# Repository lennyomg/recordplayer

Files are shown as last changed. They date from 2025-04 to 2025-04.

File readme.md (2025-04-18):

# Record Player

A real player that plays fake records.

(https://www.youtube.com/watch?v=qOQR8iDCI8Y)

This is [Owntone](https://owntone.github.io/owntone-server/) media server in retro-style body. It plays local files and streams Spotify to local speakers or Apple HomePods. Disks are NFC tags. A Python application connects the NFC reader, LED lights, input controls, and controls Owntone using its RESTful API. Everything is running on a headless Raspberry Pi with a little help from a CircuitPython development board. And a small motor inside spins a disk.

[How to build](docs/instruction.md)
[Instructables](https://www.instructables.com/Record-Player-a-Real-Player-That-Plays-Fake-Record/)
[MakerWorld](https://makerworld.com/en/models/1300993-record-player)
[YouTube](https://www.youtube.com/watch?v=qOQR8iDCI8Y)
[OnShape](https://cad.onshape.com/documents/8d49c69d5558d4a3c2d04c2c/w/57560bbfb3612a29b81fb9af/e/d4a23e81e34f632615be4a04)

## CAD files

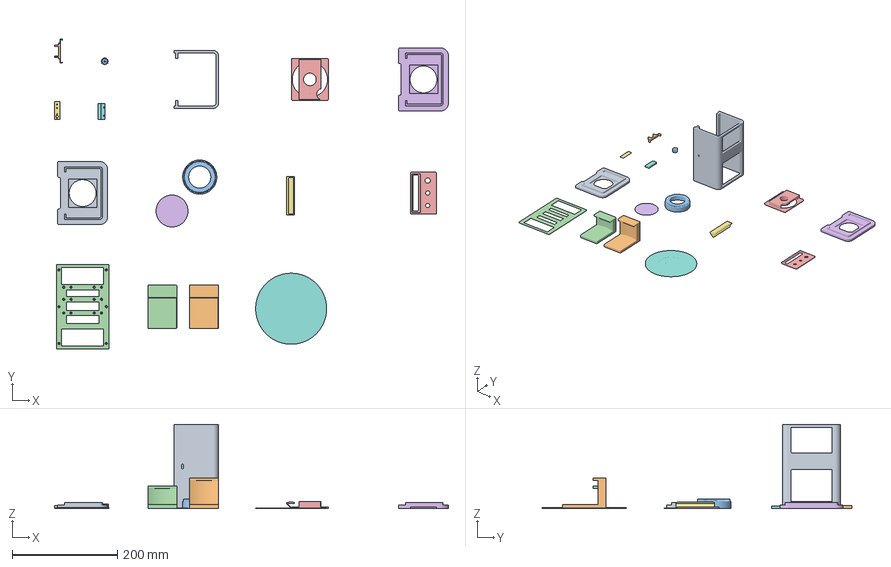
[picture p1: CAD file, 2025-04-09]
print/recordplayer.3mf
749.0 x 588.5 x 160.0 mm
side panel 2
stand 45mm
spinner gear
stand 30mm
spinner panel
spinner lid
motor mount
usb mount
main
nfc mount
motor gear
bottom
control panel
side panel 1
led diffuser
disk

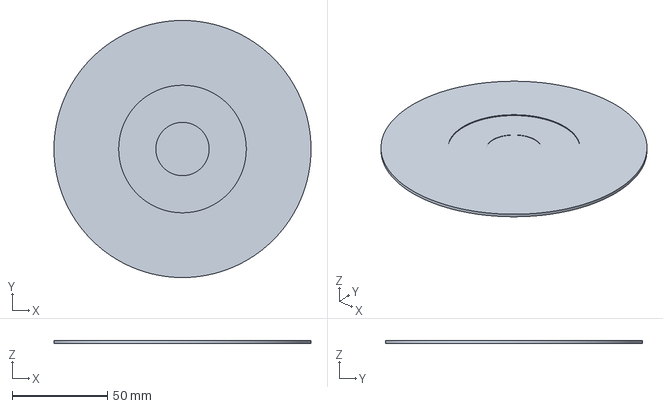
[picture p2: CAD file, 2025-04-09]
print/disk.3mf
135.0 x 135.0 x 1.50 mm

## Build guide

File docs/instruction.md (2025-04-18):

# Record Player

A real player that plays fake records.

Source on [GitHub](https://github.com/lennyomg/recordplayer).

(https://www.youtube.com/watch?v=qOQR8iDCI8Y)

This is [Owntone](https://owntone.github.io/owntone-server/) media server in retro-style body. It plays local files and streams Spotify to local speakers or Apple HomePods. Disks are NFC tags. A Python application connects the NFC reader, LED lights, input controls, and controls Owntone using its RESTful API. Everything is running on a headless Raspberry Pi with a little help from a CircuitPython development board. And a small motor inside spins a disk.

### Raspberry Pi

The shell has mounting holes for Pi Zero and Pi Model 3 A+. Pi Zero has a longer booting time, but takes up less space. Pi 3 generates more heat, but is more responsive and Wi-Fi is better. I choose Pi Zero W 2 for now. It hiccups sometimes, but I can live with that.

Get an SD card and [flash](https://www.raspberrypi.com/software/) it with Raspberry Pi OS Bookworm Lite 64-bit. I had mixed results with Bullseye. Add these two lines in config.txt to enable [SPI](https://learn.adafruit.com/circuitpython-on-raspberrypi-linux/spi-sensors-devices) and [UART](https://learn.adafruit.com/circuitpython-on-raspberrypi-linux/uart-serial).

```
dtparam=spi=on
enable_uart=1
```

### Audio

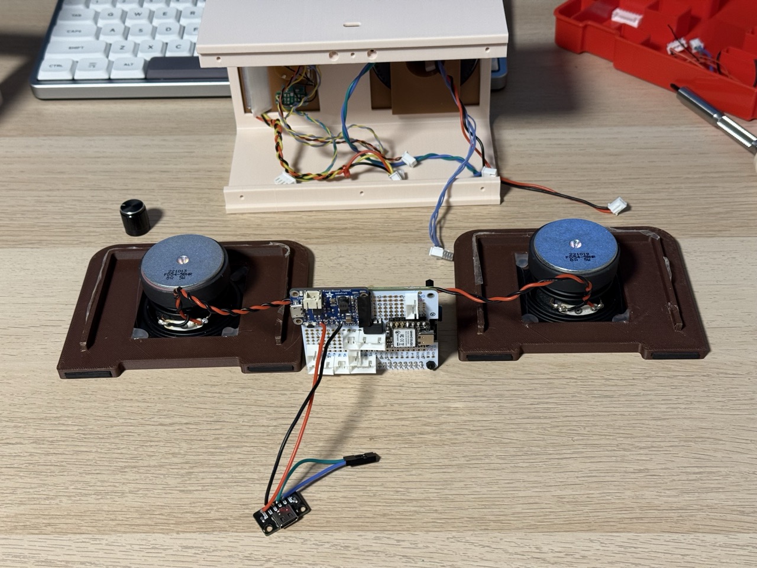
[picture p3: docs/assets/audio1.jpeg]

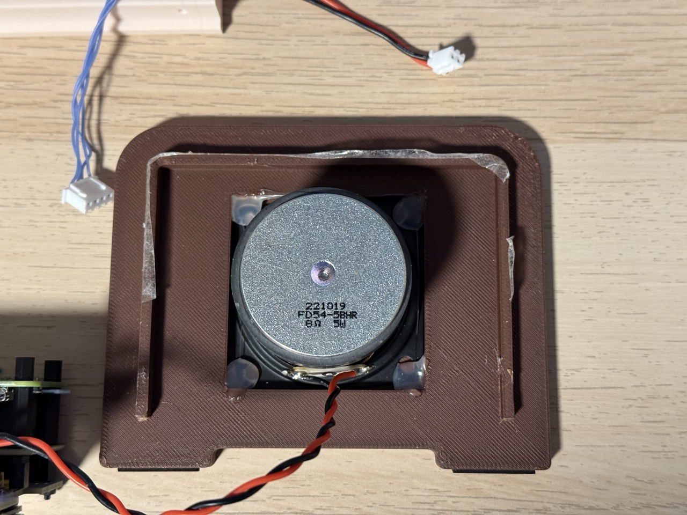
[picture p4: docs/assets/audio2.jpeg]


The Pi Model 3 A+ has a 3.5mm headphone jack, but it is no good. Audio I2S HAT is the way to go. I've got [Adafruit I2S 3W Stereo Speaker Bonnet](https://www.adafruit.com/product/3346). This [guide](https://learn.adafruit.com/adafruit-speaker-bonnet-for-raspberry-pi) should work for all I2S HATs.

As for speakers - any 3W or 5W will do. I salvaged mine from an [Amazon Basic Speaker](https://www.amazon.com/dp/B07D7TV5J3), which I had from one of my previous projects. Sound quality is... good enough. Glue the speakers into the side walls with a hot glue gun.

### Motor

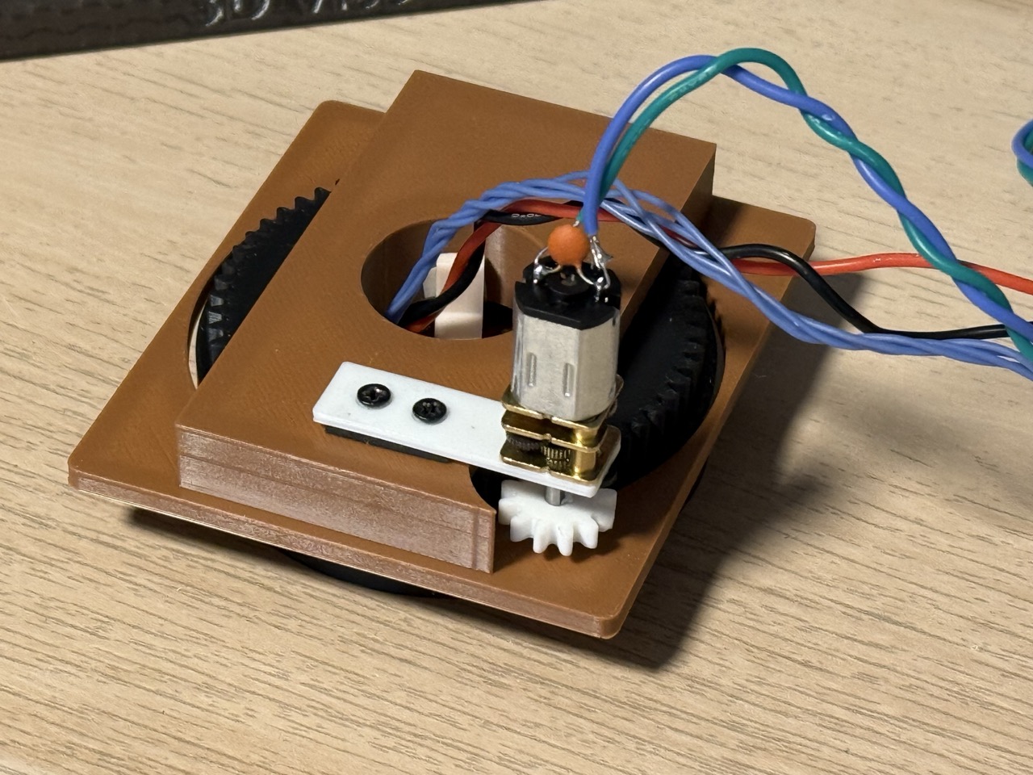
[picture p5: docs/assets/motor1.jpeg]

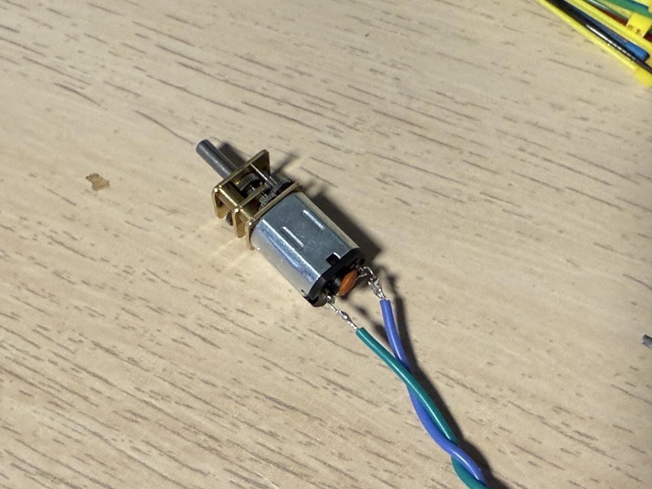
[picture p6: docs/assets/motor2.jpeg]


Take an [N20 DC motor](https://www.amazon.com/dp/B07FYBQ7Z4) that works from 6V and has a speed of 10-30 RPM. Optionally, solder a ceramic capacitor between the motor terminals to reduce noise and smooth spinning at low speeds. Do not lube the motor with liquid oil; it makes the noise worse.

To control the motor, I use [L9110H H-Bridge Motor Driver](https://www.adafruit.com/product/4489) (pay attention to the pinout in the [datasheet](https://cdn-shop.adafruit.com/product-files/4489/4489_datasheet-l9110.pdf)). It protects the Pi from back EMF and spins the motor forward and backward.

CAUTION: Never connect a DC motor directly to Pi GPIOs. It might work, but you can fry your Pi because of back EMF and high current usage.

The spinning part of the shell is connected to the panel with a [30x42x7mm bearing](https://www.amazon.com/dp/B082PXK5K9).

In case you need to print a custom gear:
*  Pitch circle diameter: 60mm and 12mm
*  Number of teeth: 60 and 12
*  Module: 1mm

The motor mount is designed to be detachable, so you can design and print your own mount and then screw it to the body with two M2 screws. Add some anti-vibration material like rubber or foam between the mount and the shell to reduce noise.

### Disks

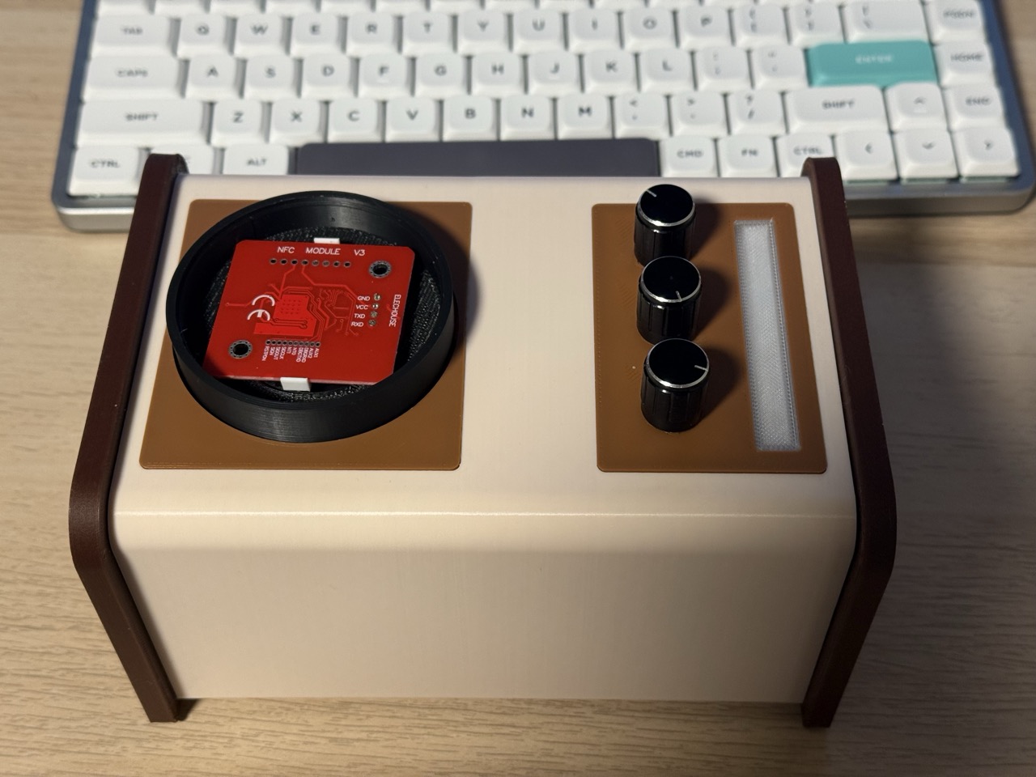
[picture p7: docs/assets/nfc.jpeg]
 
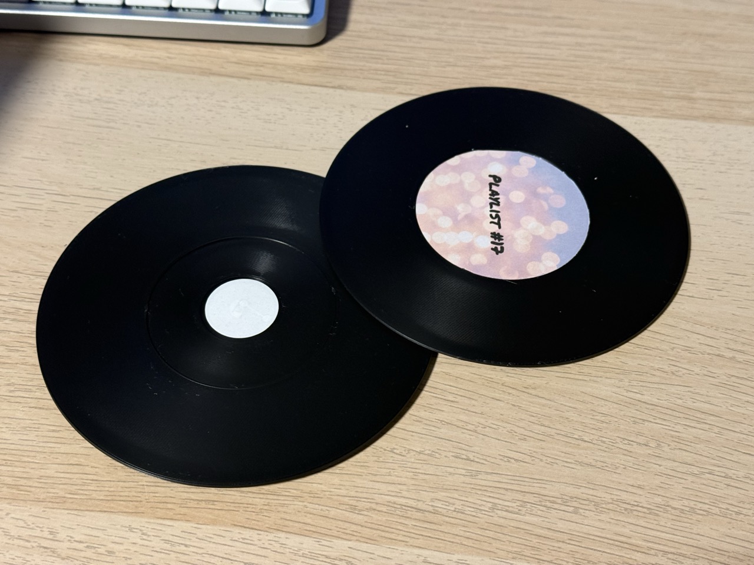
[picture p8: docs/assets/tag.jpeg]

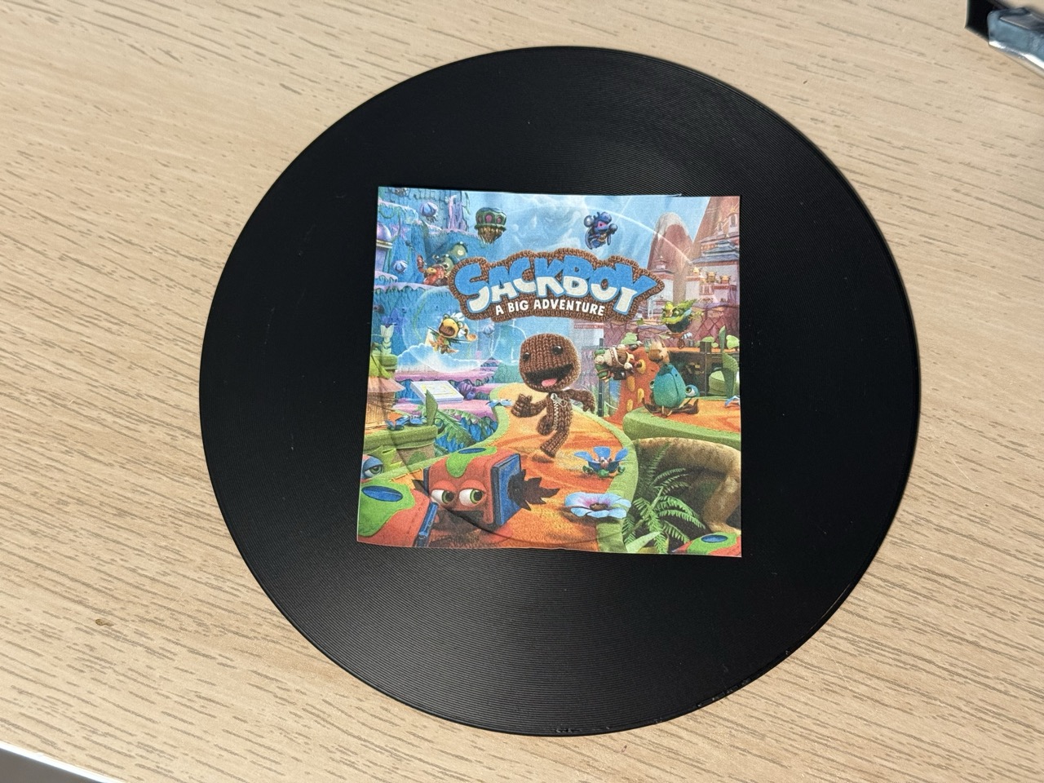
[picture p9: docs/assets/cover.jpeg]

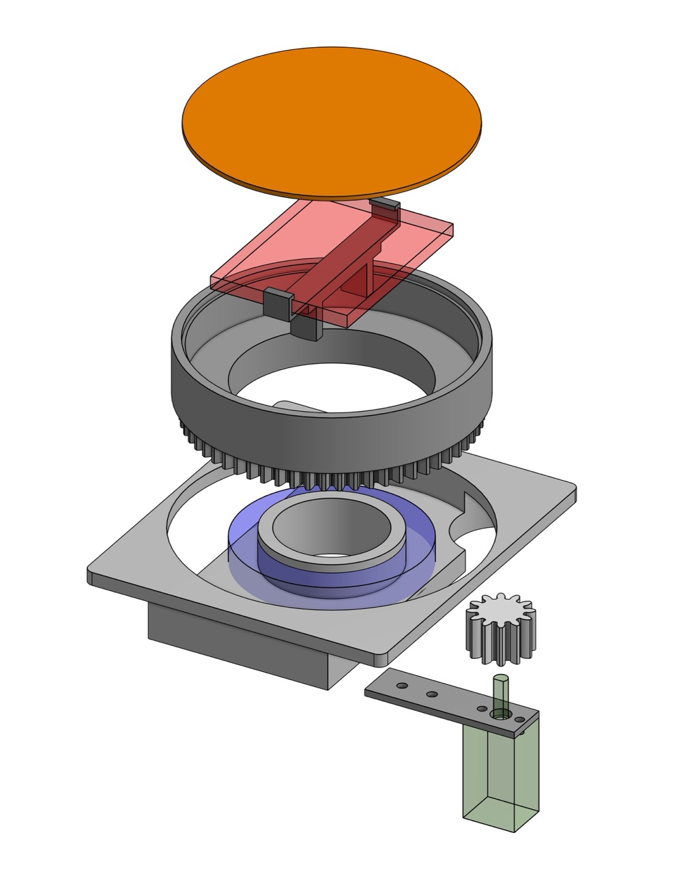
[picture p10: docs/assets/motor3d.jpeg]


This is where the magic happens. Each printed disk has [a small NFC sticker tag](https://www.amazon.com/dp/B075CFXY8V) under the cover. An NFC reader is located inside the spinning part, but the reader doesn't spin! Each tag id is associated with an album or playlist in Owntone.

PN532 is a common choice for an NFC reader, but most of them are too big for this project. I recommend [this board from HiLetgo;](https://www.amazon.com/dp/B01I1J17LC) it is small and fits nicely into the spinning part.

You must use the SPI interface with PN532. The I2C interface on this chip doesn't work reliably with Raspberry Pi because of [I2C clock stretching](https://learn.adafruit.com/working-with-i2c-devices/clock-stretching). Configure the NFC module to use SPI by physically flipping an SMB header on the PCB.

Print covers on sticky paper with a size of 70x70mm, stick them to a disk, and cut them with a razor knife.

### Controls

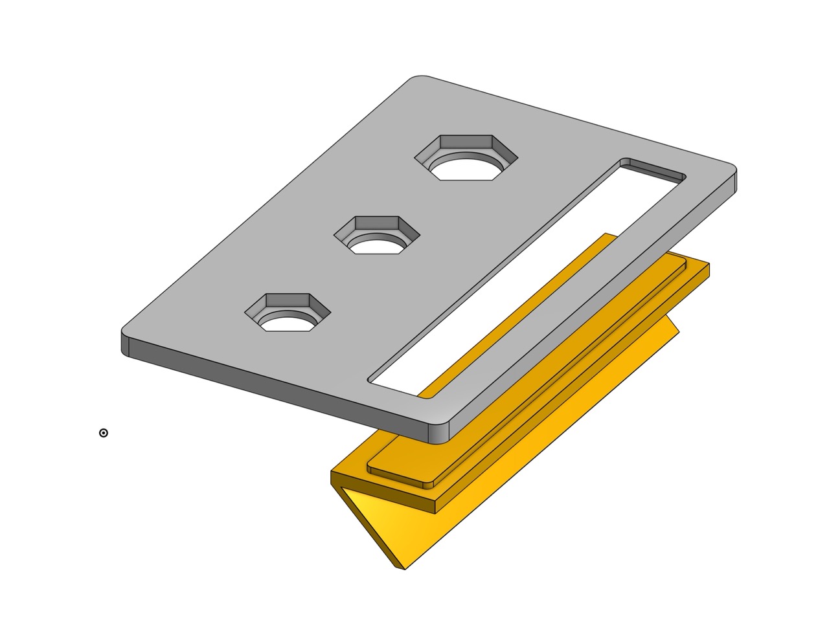
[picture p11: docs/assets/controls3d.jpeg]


Three knobs on the control panel are:

A rotary switch, ideally 1P3T. I have [2P6T](https://www.amazon.com/dp/B074WLW121) with a limiter, so it has only 3 positions:
1. Enable "turn off" for PowerBoost.
2. Select local speakers.
3. Select remote speakers.

A generic potentiometer with an internal switch, like [this one.](https://www.adafruit.com/product/3395) The potentiometer controls volume, the switch acts like mute.

A generic [rotary encoder](https://www.amazon.com/dp/B08728K3YB) for skipping tracks and play/pause.

To add some light, I cut 10 LEDs from this [WS2812B 144-LED 3.3-foot strip](https://www.amazon.com/dp/B09PBGZMNS). I think any NeoPixel strip will work. Adafruit has an [excellent guide](https://learn.adafruit.com/adafruit-neopixel-uberguide/the-magic-of-neopixels) about it.

### Power

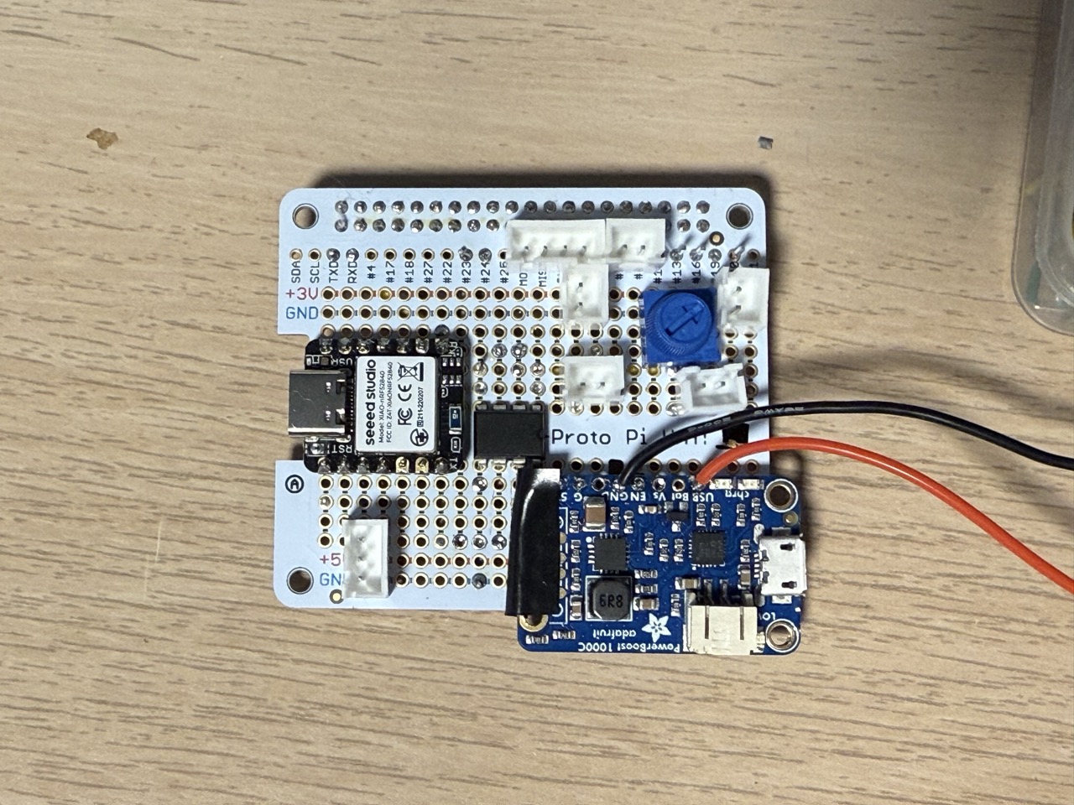
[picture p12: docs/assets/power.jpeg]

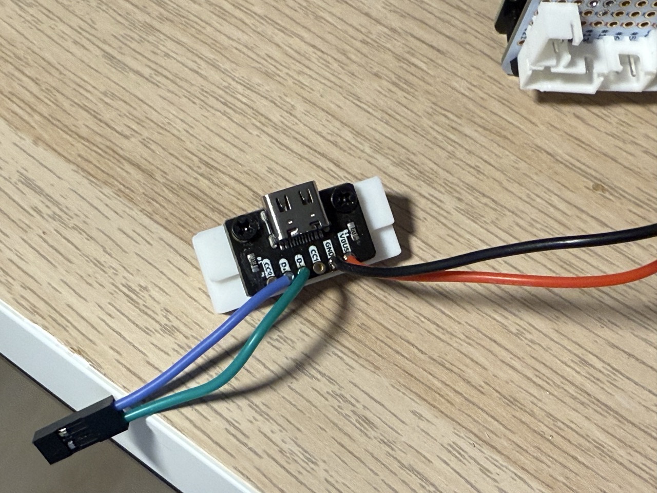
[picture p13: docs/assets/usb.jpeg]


CAUTION: Always check battery polarity with a voltmeter before connecting it.

I have a 10000 mAh Li-Po battery, but if I were you, I\'d go with 5000 mAh. [PowerBoost 1000 Charger](https://www.adafruit.com/product/2465) provides stable 5V and charges the battery fast. There are much more [affordable](https://www.adafruit.com/product/1903) options, but again, it is what I had already. The PowerBoost is connected to a [USB-C breakout with CC resistors](https://www.amazon.com/dp/B096M2HQLK). The mount for the USB breakout is a separate part, so you can design your own and print it without re-printing the whole shell.

Skip the PowerBoost if you don't need a battery. Just connect VS and GND from your USB-C connector to the Pi power pins.

### Wiring
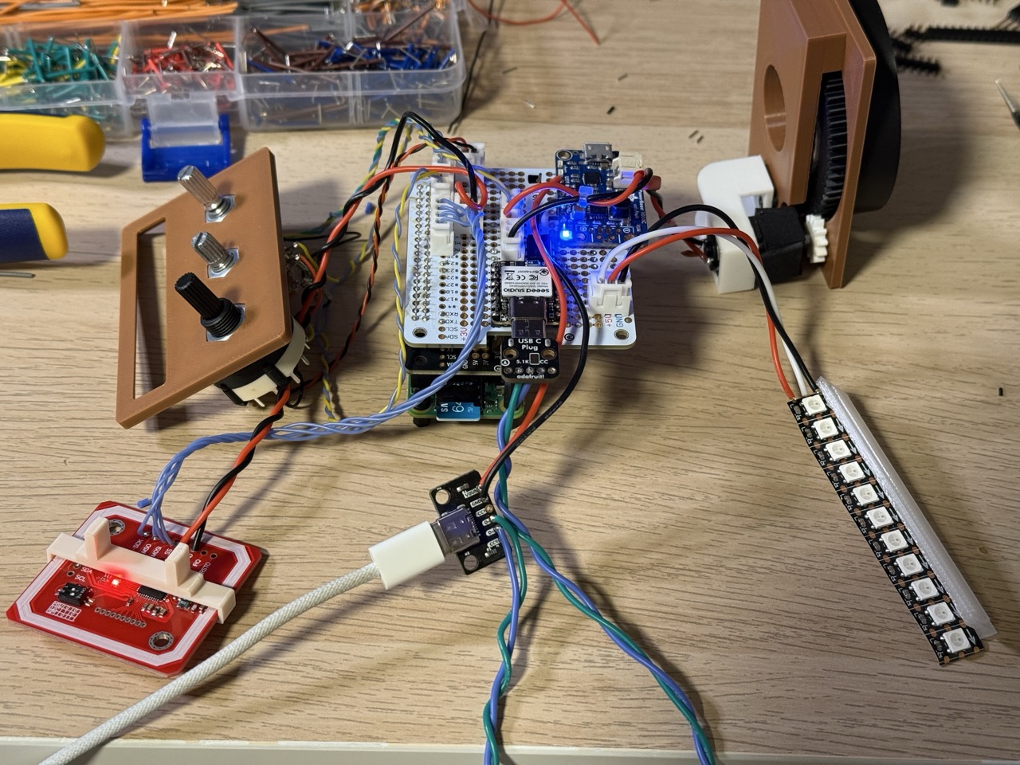
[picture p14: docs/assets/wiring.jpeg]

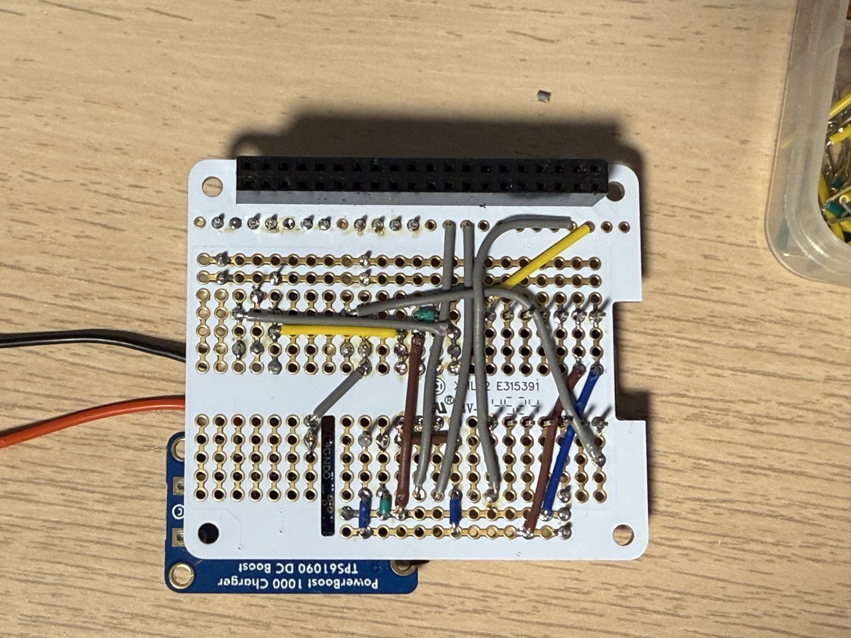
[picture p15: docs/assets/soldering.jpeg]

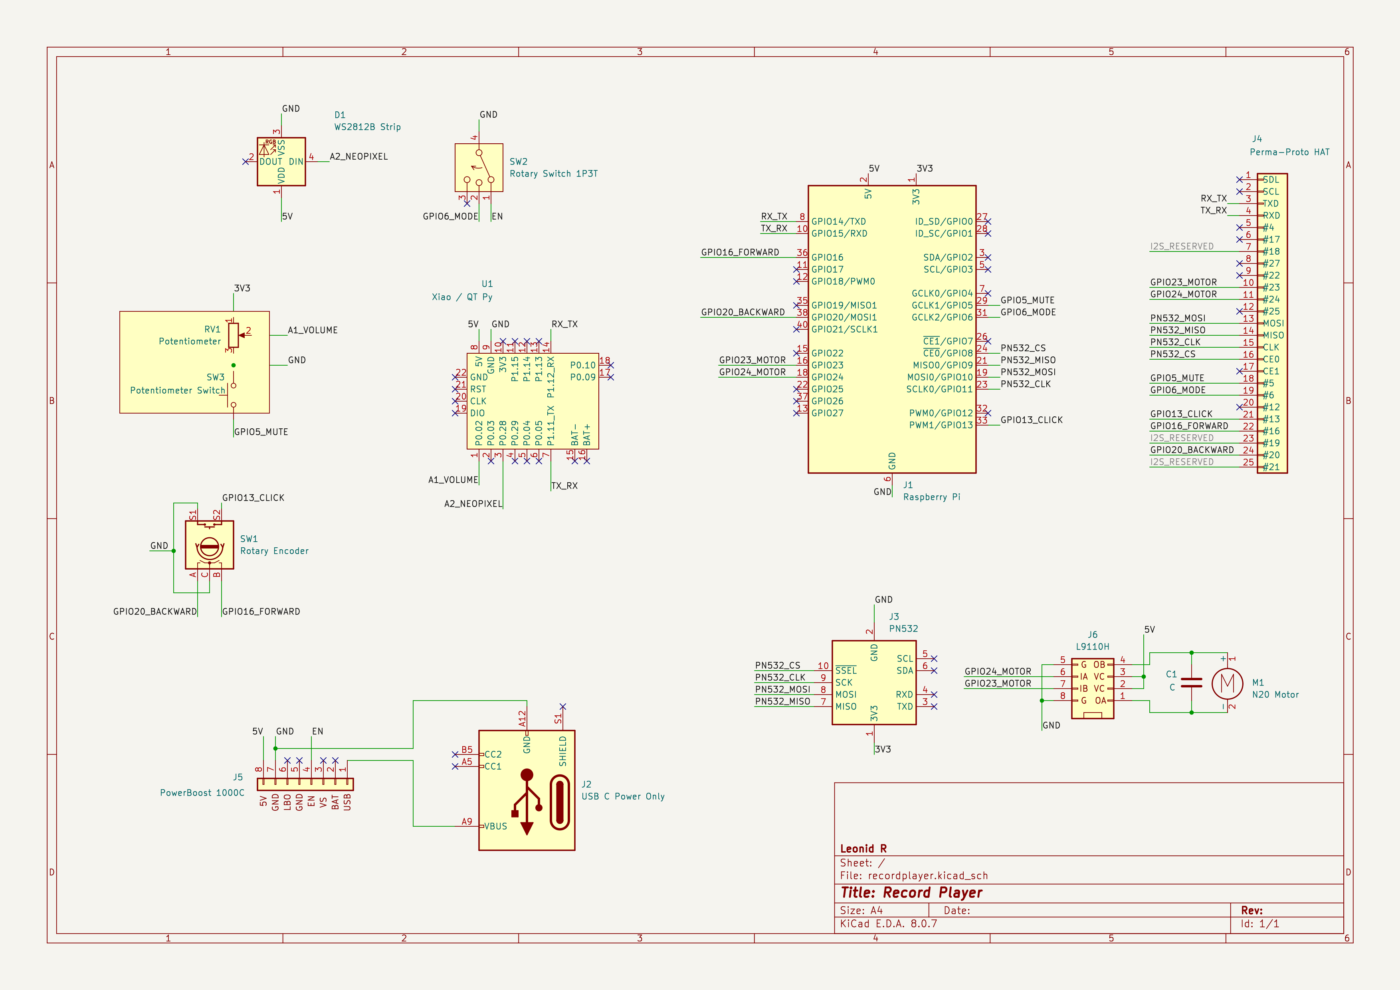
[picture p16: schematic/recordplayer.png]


[Perma-Proto](https://www.adafruit.com/product/2310) is amazing. Do yourself a favor and use JST connectors on the protoboard. It is much easier to assemble and disassemble the project this way. Carefully follow the schematic and solder everything together. Pay attention to component orientation.

Here is a list of materials I used:
* [26 AWG](https://www.amazon.com/dp/B089CZFDX2) wires for power lines and audio
* [30 AWG](https://www.amazon.com/dp/B089D31ZX6) wires for data lines
* [2.54mm JST connectors](https://www.amazon.com/dp/B09DFM29FV)
* [Jumper wires](https://www.amazon.com/dp/B08YRGVYPV) for the protoboard
* [Standoff screws](https://www.amazon.com/dp/B0BXT4FG1T)

Do not use pins #18, #19, #21 - they are reserved for I2S audio.

### Printing and assembling

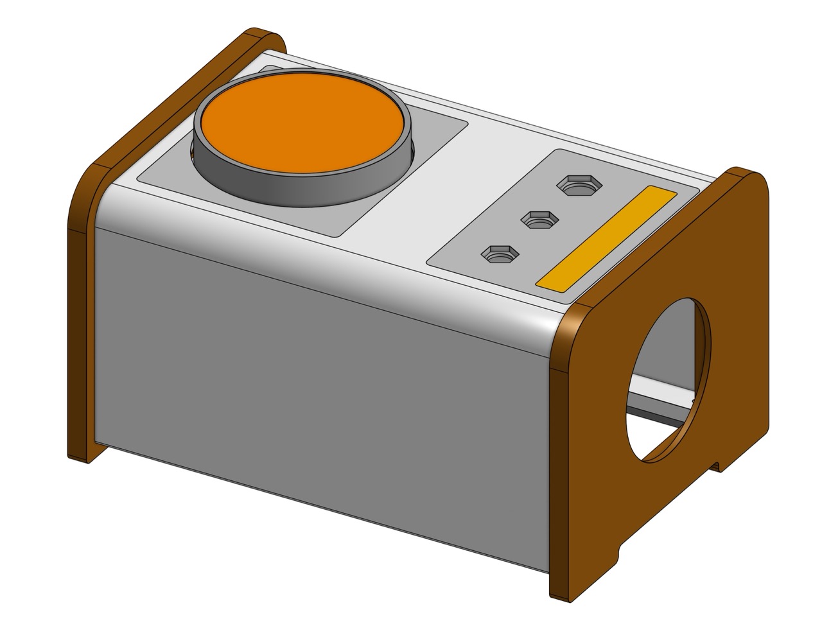
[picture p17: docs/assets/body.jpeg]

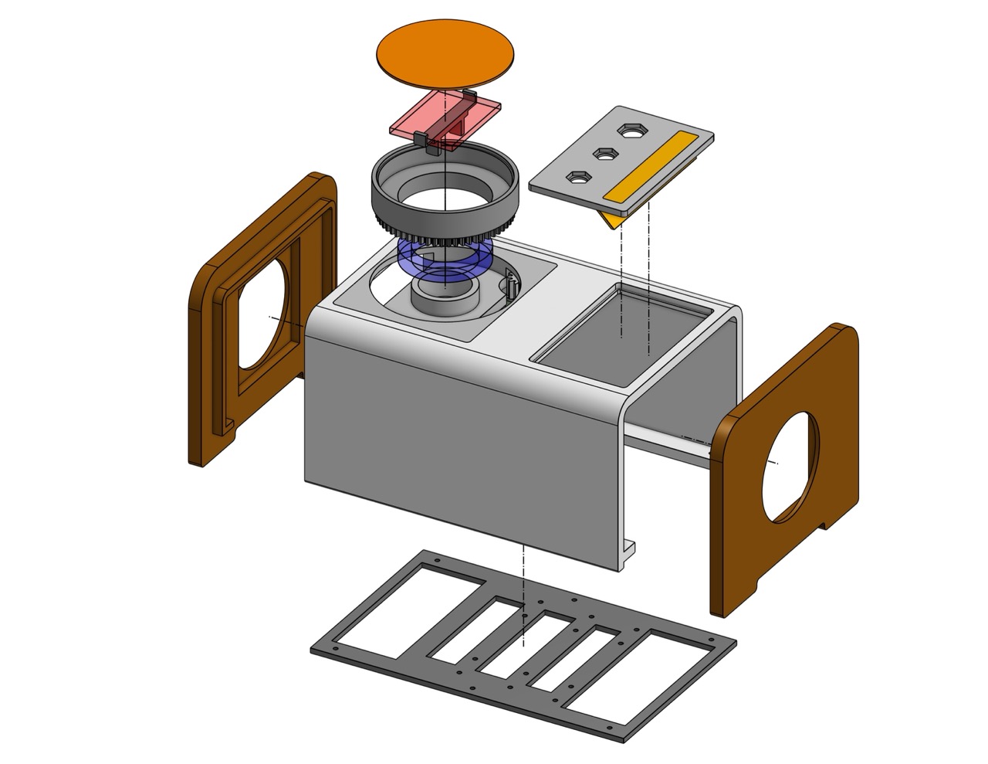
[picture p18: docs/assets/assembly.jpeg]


Main body is Basic PLA. Side panels are Bambu PLA Wood. LED defuser is translucent PETG. I printed everything in 0.16 High Quality profile with Bambu A1 Mini. Depending on body color, you may want to increase infill up to 75% (grid) to avoid light-bleeding from LEDs. Top parts must snap into place. Side walls or any other loose parts can be secured with thin double-sided tape. Bottom panel is fixed with six [M2](https://www.amazon.com/dp/B089QX453K) screws.

### Owntone

Follow Owntone [documentation](https://owntone.github.io/owntone-server/building/) on how to build and configure it. It is actually not that difficult.

Install dependencies.

```
sudo apt-get install \
  build-essential git autotools-dev autoconf automake libtool gettext gawk \
  gperf bison flex libconfuse-dev libunistring-dev libsqlite3-dev \
  libavcodec-dev libavformat-dev libavfilter-dev libswscale-dev libavutil-dev \
  libasound2-dev libxml2-dev libgcrypt20-dev libavahi-client-dev zlib1g-dev \
  libevent-dev libplist-dev libsodium-dev libjson-c-dev libwebsockets-dev \
  libcurl4-openssl-dev libprotobuf-c-dev
```

Clone repository.

```
cd \~
git clone https://github.com/owntone/owntone-server.git
cd owntone-server
```

Instead of building from the master branch, switch to a release using tags.

```
git switch 2.8.2
```

Build.

```
autoreconf -i
./configure --prefix=/usr --sysconfdir=/etc --localstatedir=/var --enable-install-user
make
sudo make install
```

Go through the config file and update settings according to your needs.

```
sudo nano /etc/owntone.conf
```

I only changed Spotify settings.

```
spotify {
  bitrate = 3
  base_playlist_disable = true
  artist_override = true
  album_override = true
}
```

Create music folder.

```
mkdir /srv/music
sudo chmod -R 777 /srv/music
```

Enable Owntone service.

```
sudo systemctl enable owntone.service
sudo systemctl start owntone.service
```

Now Owntone should be available at `http://<pi-host-name>:3689`.

### Spotify

In Owntone interface, you should log in to Spotify, as it is described in [the official guide](https://owntone.github.io/owntone-server/integrations/spotify/). Every time OwnTone is started (every time you turn on Pi), it loads all saved playlists from Spotify; it surely takes time. I use a dedicated account in the family plan with only playlists I listen to.

### Satellite board

Take one of [Seeed XIAO](https://www.seeedstudio.com/test-for-xiao.html) or [Adafruit QT Py](https://www.adafruit.com/category/595) boards just because they are small. RP2040-based boards usually cost less. I use XIAO nRF52840 in this project. The board does two things: controls NeoPixel LED strip and reads analog input. Also, as the board starts instantly, I can now play a LED animation while the Pi is booting.

Flash your board with CircuitPython firmware, find the right one on [circuitpython.org](http://circuitpython.org). It should be detected as a thumb drive when connected to a computer. Learn more on [Adafruit](https://learn.adafruit.com/welcome-to-circuitpython/what-is-circuitpython).

Install libraries to the board (run on your computer, not on the Pi).

```
pip install circup
circup install neopixel
circup install adafruit_led_animation
circup install adafruit_ticks
circup install adafruit_led_animation
```

Now copy Python files from src/board to the board, and it is done.

CAUTION: Do not connect the board to your computer while it is powered by another power source. You may back-power the USB controller inside your computer and burn it.

### Control app

Copy everything from `src` to `~/recordplayer` on the Pi.

Activate environment.

```
cd ~/recordplayer
sudo apt install python3-dev libgpiod-dev python3-libgpiod 
python -m venv .venv
source .venv/bin/activate
pip install -r requirements.txt
sudo chmod 777 ./run
echo @reboot ~/recordplayer/run | crontab -
```

Find available speakers and outputs.
```
python pi/outputs.py
```
Insert IDs of remote speakers that you want to use into OUTPUTS in `playback.py`. Keep \"0\" - it is for local speakers.

```
OUTPUTS = [
    ["0"],
    ["remote_output_id", "another_remote_id_if_any"],
]
```

Test it.

```
./run
```

### Library

In `library.py`, you find a list of NFC tag IDs with associated
playlists and albums.

```
playlists = {
    "rfid_id": {
        "uris": "library:album:123456789",
        "shuffle": "false",
    },
    "04422601654003": {
        "uris": "spotify:playlist:37i9dQZF1DWUrmUI5ur5GK",
        "shuffle": "true"
    },
}
```

Place NFC tag on the reader, run the command below, and you will see the tag ID. Copy it and use it in `library.py`.

```
journalctl /usr/bin/python
```

Spotify URIs are regular Spotify URIs; you can find them in Owntone UI.

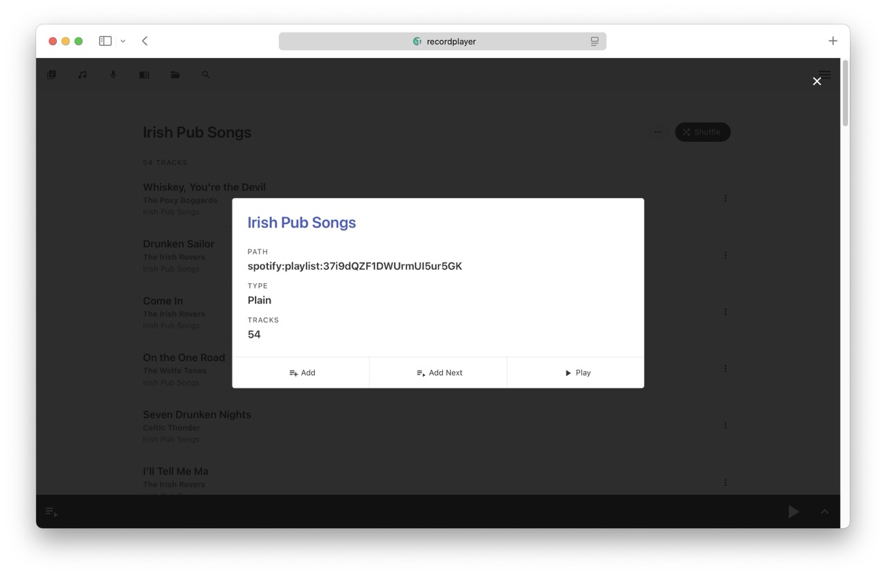
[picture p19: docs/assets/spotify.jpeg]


Owntone doesn't show URIs for albums; you need to extract it from the URL. Open an album in a browser, copy the URL, and change it from `http://recordplayer:3689/#/music/albums/8249546791409011466` to `library:album:8249546791409011466`.

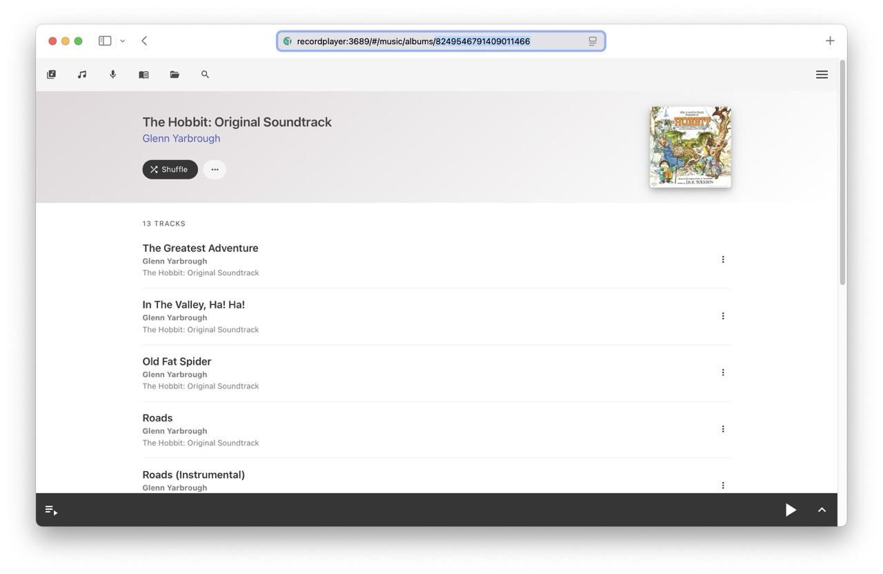
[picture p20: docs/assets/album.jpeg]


Restart Pi after making changes in `library.py`.

### Conclusion

Done. Enjoy.

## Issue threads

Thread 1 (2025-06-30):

Problems getting PN532 detected?

slooker, 2025-06-30:
Did you have any issues getting the PN532 to be detected? I've tried two PN532 boards and neither one of them is detected by my Pi Zero 2W. I've added the `enable_uart=1` and `dtparam=spi=on` in the /boot/firmware/config.txt. I made sure the switches were toggled correctly (and tried the opposite way to make sure). I've even connected them directly to the pi to test.

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

lennyomg, 2025-07-04:
It is hard to see on the photo, but it looks like two switches on the board are at the same position. For SPI, one switch must be on, another must be off.

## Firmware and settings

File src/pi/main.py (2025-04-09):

import light
import motor
import playback
import syslog
from threading import Thread, Event
from traceback import format_exc

stop_event = Event()


def thread(func):
    try:
        func()
    except:
        e = format_exc()
        print(e)
        syslog.syslog(syslog.LOG_ERR, e)
        stop_event.set()


try:
    playback.init()
    Thread(target=lambda: thread(playback.daemon_control), daemon=True).start()
    Thread(target=lambda: thread(playback.daemon_rfid), daemon=True).start()
    stop_event.wait()
finally:
    light.error()
    motor.stop()

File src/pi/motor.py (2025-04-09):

import board
import pwmio

PWM_FREQUENCY = 30
PWM_DUTY_CYCLE_SLOW = 5000
PWM_DUTY_CYCLE_FAST = 20000
PIN_FORWARD = board.D24
PIN_BACKWARD = board.D23

motor_forward = pwmio.PWMOut(PIN_FORWARD, frequency=PWM_FREQUENCY)
motor_backward = pwmio.PWMOut(PIN_BACKWARD, frequency=PWM_FREQUENCY)


def backward():
    motor_backward.duty_cycle = PWM_DUTY_CYCLE_FAST
    motor_forward.duty_cycle = 0


def forward(speed=PWM_DUTY_CYCLE_SLOW):
    motor_forward.duty_cycle = speed
    motor_backward.duty_cycle = 0


def stop():
    motor_backward.duty_cycle = 0
    motor_forward.duty_cycle = 0


if __name__ == "__main__":
    forward()
    while True:
        pass

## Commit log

2025-04-09 initial implementation
    [disk.3mf, recordplayer.kicad_sch, shell.3mf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]
2025-04-09 post-publish fixes
    [recordplayer.3mf, shell.3mf, stand.3mf]
